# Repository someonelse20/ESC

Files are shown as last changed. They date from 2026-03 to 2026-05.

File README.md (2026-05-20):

# ESC

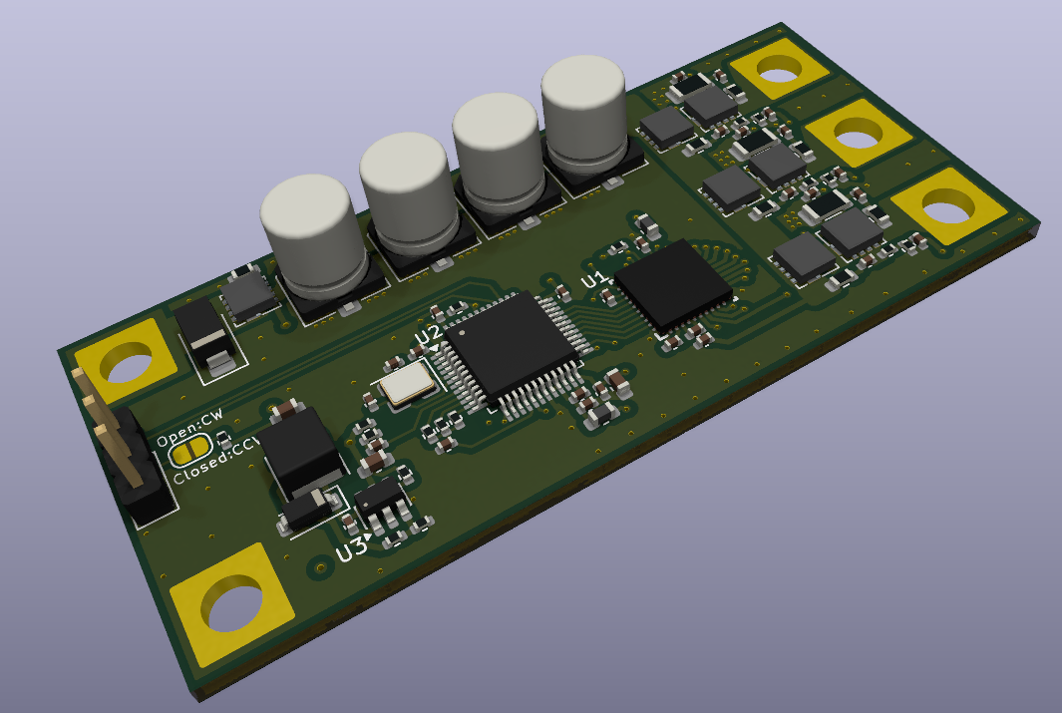
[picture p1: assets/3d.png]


A custom designed electronic speed controller that supports up to 7 cell LiPo batteries with 30 amps (untested).
I made this as part of my overall project of making a drone from scratch.

## Pinout

| Pin # | Function  |
| ----- | --- |
| 1 | PWM IN |
| 2 | Direction |
| 3 | GND |

Pull the Direction pin low (default) for clockwise rotation or high (3.3v) for counter clockwise rotation.
Alternatively, leave the solder bridge on the bottom of the board open for clockwise and closed for counter clockwise.

## PCB Layout

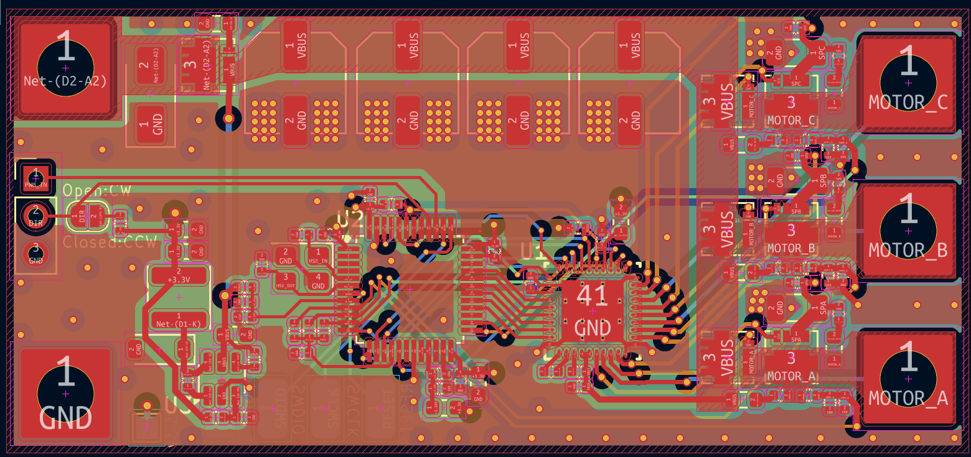
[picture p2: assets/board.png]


## Schematic

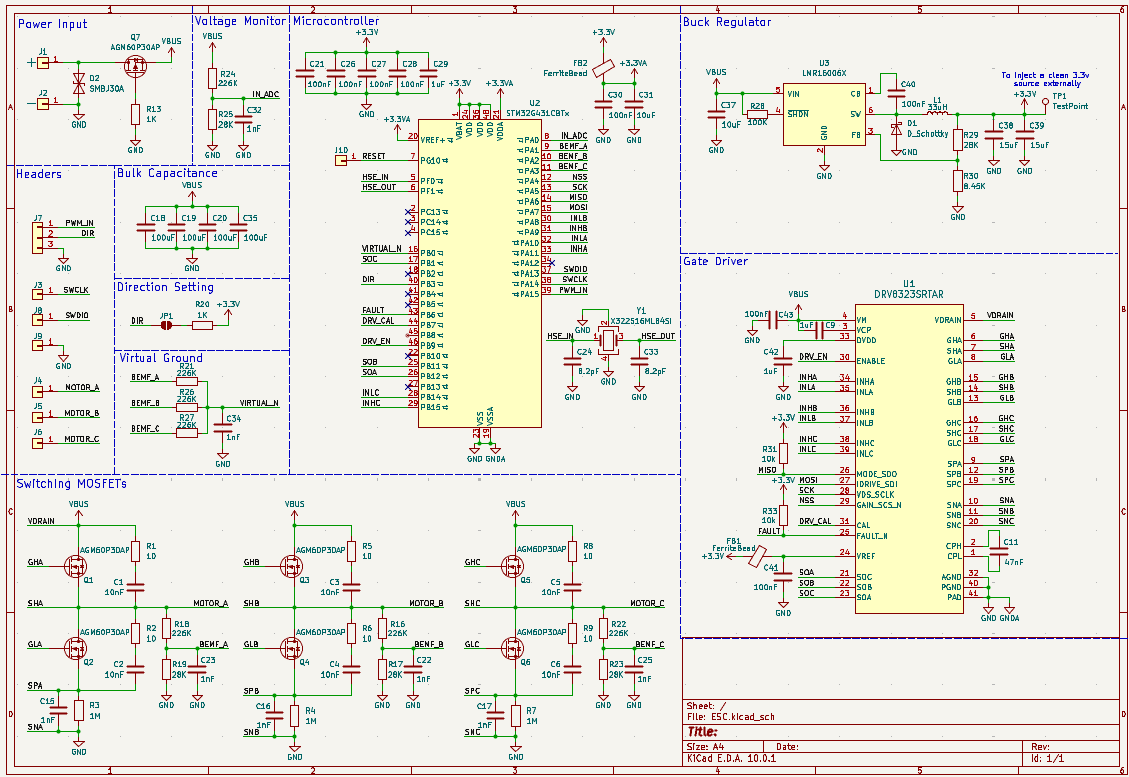
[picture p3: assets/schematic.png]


## BOM

| Name | Purpose | Quantity | Total Cost (USD) | Link | Distributor |
| --- | --- | --- | --- | --- | --- |
| PCB | 	The Circuit Board | 5 | 7.00 | [JLCPCB](https://jlcpcb.com/) | JLCPCB |
| PCB Assembly | Assembly for the board | 2 | 78.46 | [JLCPCB](https://jlcpcb.com/) | JLCPCB |

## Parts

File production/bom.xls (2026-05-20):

JLCPCB BOM Tool - BOM Matching
BOM name：bom-JLCPCB Assembly Order.xlsx |  |  | Download Time：2026-05-20 23:46:29 |  |  |  | * Our matching results are updated in real-time, but stock and prices may change. If it's been over 24 hours, please re-match before placing your order.
PCB Assembled Qty：5 |  |  | Est. Total Price：20.6320
Your BOM |  |  |  |  | Matched Parts |  |  |  |  |  |  | Order Information
Top Designator | Bottom Designator | Comment | Footprint | JLCPCB Part # | Matches | Part # | Manufacturer | Footprint | Description | Category | Warning | JLCPCB Part # | Product link | Lib Type | Qty | Source | Total Price ($)
C1,C2,C3,C4,C5,C6 |  | 10nF | 0402 |  | Select by System | CL05B103KB5NNNC | Samsung Electro-Mechanics | 0402 | 10nF 50V X7R ±10% 0402 Multilayer Ceramic Capacitors MLCC - SMD/SMT ROHS | Multilayer Ceramic Capacitors MLCC - SMD/SMT |  | C15195 | https://jlcpcb.com/partdetail/15869-CL05B103KB5NNNC/C15195 | Basic | 12 | 12 JLCPCB | 0.0192
C11 |  | 47nF | 0402 |  | Select by System | 0402B473K500NT | FH (Guangdong Fenghua Advanced Tech) | 0402 | 47nF 50V X7R ±10% 0402 Multilayer Ceramic Capacitors MLCC - SMD/SMT ROHS | Multilayer Ceramic Capacitors MLCC - SMD/SMT |  | C82219 | https://jlcpcb.com/partdetail/83376-0402B473K500NT/C82219 | Extended | 20 | 20 JLCPCB | 0.04
C15,C16,C17,C22,C23,C25,C32,C34 |  | 1nF | 0402 |  | Select by System | 0402B102K500NT | FH (Guangdong Fenghua Advanced Tech) | 0402 | 1nF 50V X7R ±10% 0402 Multilayer Ceramic Capacitors MLCC - SMD/SMT ROHS | Multilayer Ceramic Capacitors MLCC - SMD/SMT |  | C1523 | https://jlcpcb.com/partdetail/1875-0402B102K500NT/C1523 | Basic | 16 | 16 JLCPCB | 0.0208
C18,C19,C20,C35 |  | 100uF | C_Elec_6.3x7.7 |  | Select by Customer | RVT1V101M0607 | Honor Elec | SMD,D6.3xL7.7mm | -55℃~+105℃ 100uF 2000hrs@105℃ 35V 6.3mm 7.7mm ±20% SMD,D6.3xL7.7mm Aluminum Electrolytic Capacitors - SMD ROHS | Aluminum Electrolytic Capacitors - SMD |  | C3339 | https://jlcpcb.com/partdetail/HonorElec-RVT1V101M0607/C3339 | Extended | 10 | 10 JLCPCB | 0.377
C21,C26,C27,C28,C30,C40,C41,C43 |  | 100nF | 0402 |  | Select by Customer | GMK105BJ104KV-F | Taiyo Yuden | 0402 | 100nF 35V X5R ±10% 0402 Multilayer Ceramic Capacitors MLCC - SMD/SMT ROHS | Multilayer Ceramic Capacitors MLCC - SMD/SMT |  | C187828 | https://jlcpcb.com/partdetail/TaiyoYuden-GMK105BJ104KVF/C187828 | Extended | 24 | 24 JLCPCB | 0.1344
C24,C33 |  | 8.2pF | 0402 |  | Select by System | 0402CG8R2C500NT | FH (Guangdong Fenghua Advanced Tech) | 0402 | 50V 8.2pF C0G 0402 Multilayer Ceramic Capacitors MLCC - SMD/SMT ROHS | Multilayer Ceramic Capacitors MLCC - SMD/SMT |  | C1579 | https://jlcpcb.com/partdetail/1931-0402CG8R2C500NT/C1579 | Extended | 20 | 20 JLCPCB | 0.026
C29 |  | 1uF | 0603 |  | Select by System | CL10A105KB8NNNC | Samsung Electro-Mechanics | 0603 | 1uF 50V X5R ±10% 0603 Multilayer Ceramic Capacitors MLCC - SMD/SMT ROHS | Multilayer Ceramic Capacitors MLCC - SMD/SMT |  | C15849 | https://jlcpcb.com/partdetail/16531-CL10A105KB8NNNC/C15849 | Basic | 2 | 2 JLCPCB | 0.0152
C31 |  | 10uF | 0402 |  | Select by System | CL05A106MQ5NUNC | Samsung Electro-Mechanics | 0402 | 10uF 6.3V X5R ±20% 0402 Multilayer Ceramic Capacitors MLCC - SMD/SMT ROHS | Multilayer Ceramic Capacitors MLCC - SMD/SMT |  | C15525 | https://jlcpcb.com/partdetail/16204-CL05A106MQ5NUNC/C15525 | Basic | 2 | 2 JLCPCB | 0.0136
C37 |  | 10uF | 0603 |  | Select by System | CL10A106KP8NNNC | Samsung Electro-Mechanics | 0603 | 10V 10uF X5R ±10% 0603 Multilayer Ceramic Capacitors MLCC - SMD/SMT ROHS | Multilayer Ceramic Capacitors MLCC - SMD/SMT |  | C19702 | https://jlcpcb.com/partdetail/20411-CL10A106KP8NNNC/C19702 | Basic | 2 | 2 JLCPCB | 0.0204
C38,C39 |  | 15uF | 0603 |  | Select by System | C1608X5R0J156MT000E | TDK | 0603 | 15uF 6.3V X5R ±20% 0603 Multilayer Ceramic Capacitors MLCC - SMD/SMT ROHS | Multilayer Ceramic Capacitors MLCC - SMD/SMT |  | C445715 | https://jlcpcb.com/partdetail/TDK-C1608X5R0J156MT000E/C445715 | Extended | 6 | 6 JLCPCB | 0.501
C42,C9 |  | 1uF | 0402 |  | Select by Customer | CL05A105KL5NRNC | Samsung Electro-Mechanics | 0402 | 1uF 35V X5R ±10% 0402 Multilayer Ceramic Capacitors MLCC - SMD/SMT ROHS | Multilayer Ceramic Capacitors MLCC - SMD/SMT |  | C307413 | https://jlcpcb.com/partdetail/291087-CL05A105KL5NRNC/C307413 | Extended | 20 | 20 JLCPCB | 0.34
D1 |  | D_Schottky | D_SOD-123 |  | Select by Customer | PMEG6010CEH,115 | Nexperia | SOD-123F | 1 Independent 1A 50uA@60V 60V 660mV@1A 9A SOD-123F Schottky Diodes ROHS | Schottky Diodes |  | C110797 | https://jlcpcb.com/partdetail/Nexperia-PMEG6010CEH115/C110797 | Extended | 6 | 6 JLCPCB | 2.0862
D2 |  | SMBJ30A | D_SMA |  | Select by System | SMBJ30A | YFW | DO-214AA(SMB) | -65℃~+150℃ 12.4A 1uA 30V 36.8V 390pF 48.4V 600W@10/1000us TVS Unidirectional DO-214AA(SMB) ESD and Surge Protection (TVS/ESD) ROHS | ESD And Surge Protection (TVS/ESD) |  | C3013760 | https://jlcpcb.com/partdetail/YFW-SMBJ30A/C3013760 | Extended | 6 | 6 JLCPCB | 0.2886
FB1,FB2 |  | FerriteBead | 0603 |  | Select by Customer | GZ1608D601TF | Sunlord | 0603 | -55℃~+125℃ 1 200mA 450mΩ 600Ω@100MHz ±25% 0603 Ferrite Beads ROHS | Ferrite Beads |  | C1002 | https://jlcpcb.com/partdetail/Sunlord-GZ1608D601TF/C1002 | Basic | 4 | 4 JLCPCB | 0.0744
L1 |  | 27uH | L_APV_ANR4030 |  | Select by Customer | ANR4030T330M | APV | SMD,4x4mm | 1.2A 33uH 920mA Magnetic Shielded Inductor ±20% SMD,4x4mm Power Inductors ROHS | Power Inductors |  | C7497082 | https://jlcpcb.com/partdetail/APV-ANR4030T330M/C7497082 | Extended | 5 | 5 JLCPCB | 0.214
Q1,Q2,Q3,Q4,Q5,Q6 |  | AGM60P30AP | D_QFN_3.3x3.3mm_P0.65mm |  | Unconfirmed | AGM60P30AP | AGM-Semi | PDFN-8(3.3x3.3) | -55℃~+150℃ 1 P-Channel 1.6V 114pF 11pF 30A 35W 40mΩ@10V 60V 740pF 9.8nC@10V P-Channel PDFN-8(3.3x3.3) MOSFETs ROHS | MOSFETs | 1.Multiple lines in the BOM have been matched to the same part. Please check if the matching is correct. ; | C20625923 | https://jlcpcb.com/partdetail/AGMSemi-AGM60P30AP/C20625923 | Extended | 14 | 14 JLCPCB | 2.6096
Q7 |  | AGM60P30A | D_QFN_3.3x3.3mm_P0.65mm |  | Select by Customer | AGM60P30AP | AGM-Semi | PDFN-8(3.3x3.3) | -55℃~+150℃ 1 P-Channel 1.6V 114pF 11pF 30A 35W 40mΩ@10V 60V 740pF 9.8nC@10V P-Channel PDFN-8(3.3x3.3) MOSFETs ROHS | MOSFETs | 1.Multiple lines in the BOM have been matched to the same part. Please check if the matching is correct. ; | C20625923 | https://jlcpcb.com/partdetail/AGMSemi-AGM60P30AP/C20625923 | Extended | 14 | 14 JLCPCB | 2.6096
R1,R2,R5,R6,R8,R9 |  | 10 | 0603 |  | Unconfirmed | 0603WAF100JT5E | UNI-ROYAL(Uniroyal Elec) | 0603 | -55℃~+155℃ 100mW 10Ω 75V Thick Film Resistor ±1% ±400ppm/℃ 0603 Chip Resistor - Surface Mount ROHS | Chip Resistor - Surface Mount | 1.The comment (0603WAF100JT5E) of this part does not match the one (10) provided in your BOM. Please confirm; | C22859 | https://jlcpcb.com/partdetail/23586-0603WAF100JT5E/C22859 | Basic | 12 | 12 JLCPCB | 0.0228
R3,R4,R7 |  | 1M | 1206 |  | Unconfirmed | 1206W4F1004T5E | UNI-ROYAL(Uniroyal Elec) | 1206 | -55℃~+155℃ 1MΩ 200V 250mW Thick Film Resistor ±1% ±100ppm/℃ 1206 Chip Resistor - Surface Mount ROHS | Chip Resistor - Surface Mount | 1.The comment (1206W4F1004T5E) of this part does not match the one (1M) provided in your BOM. Please confirm; | C17927 | https://jlcpcb.com/partdetail/18615-1206W4F1004T5E/C17927 | Basic | 6 | 6 JLCPCB | 0.0258
R13 |  | 1K | 0603 |  | Unconfirmed | 0603WAF1001T5E | UNI-ROYAL(Uniroyal Elec) | 0603 | -55℃~+155℃ 100mW 1kΩ 75V Thick Film Resistor ±1% ±100ppm/℃ 0603 Chip Resistor - Surface Mount ROHS | Chip Resistor - Surface Mount | 1.The comment (0603WAF1001T5E) of this part does not match the one (1K) provided in your BOM. Please confirm; | C21190 | https://jlcpcb.com/partdetail/21904-0603WAF1001T5E/C21190 | Basic | 2 | 2 JLCPCB | 0.0032
R16,R18,R21,R22,R24,R26,R27 |  | 226K | 0402 |  | Unconfirmed | CR0402FF2263G | LIZ Elec | 0402 | -55℃~+125℃ 226kΩ 50V 62.5mW Thick Film Resistor ±1% ±200ppm/℃ 0402 Chip Resistor - Surface Mount ROHS | Chip Resistor - Surface Mount | 1.The comment (CR0402FF2263G) of this part does not match the one (226K) provided in your BOM. Please confirm; | C100317 | https://jlcpcb.com/partdetail/LIZElec-CR0402FF2263G/C100317 | Extended | 24 | 24 JLCPCB | 0.0144
R17,R19,R23,R25,R29 |  | 28K | 0402 |  | Unconfirmed | FRC0402F2802TS | FOJAN | 0402 | -55℃~+155℃ 28kΩ 50V 62.5mW Thick Film Resistor ±1% ±100ppm/℃ 0402 Chip Resistor - Surface Mount ROHS | Chip Resistor - Surface Mount | 1.The comment (FRC0402F2802TS) of this part does not match the one (28K) provided in your BOM. Please confirm; | C2998150 | https://jlcpcb.com/partdetail/FOJAN-FRC0402F2802TS/C2998150 | Extended | 20 | 20 JLCPCB | 0.012
R20 |  | 1K | 0402 |  | Unconfirmed | 0402WGF1001TCE | UNI-ROYAL(Uniroyal Elec) | 0402 | -55℃~+155℃ 1kΩ 50V 62.5mW Thick Film Resistor ±1% ±100ppm/℃ 0402 Chip Resistor - Surface Mount ROHS | Chip Resistor - Surface Mount | 1.The comment (0402WGF1001TCE) of this part does not match the one (1K) provided in your BOM. Please confirm; | C11702 | https://jlcpcb.com/partdetail/12256-0402WGF1001TCE/C11702 | Basic | 2 | 2 JLCPCB | 0.002
R28 |  | 100K | 0402 |  | Unconfirmed | 0402WGF1003TCE | UNI-ROYAL(Uniroyal Elec) | 0402 | -55℃~+155℃ 100kΩ 50V 62.5mW Thick Film Resistor ±1% ±100ppm/℃ 0402 Chip Resistor - Surface Mount ROHS | Chip Resistor - Surface Mount | 1.The comment (0402WGF1003TCE) of this part does not match the one (100K) provided in your BOM. Please confirm; | C25741 | https://jlcpcb.com/partdetail/26484-0402WGF1003TCE/C25741 | Basic | 2 | 2 JLCPCB | 0.0018
R30 |  | 8.45K | 0402 |  | Unconfirmed | RC0402FR-078K45L | YAGEO | 0402 | -55℃~+155℃ 50V 62.5mW 8.45kΩ Thick Film Resistor ±1% ±100ppm/℃ 0402 Chip Resistor - Surface Mount ROHS | Chip Resistor - Surface Mount | 1.The comment (RC0402FR-078K45L) of this part does not match the one (8.45K) provided in your BOM. Please confirm; | C185388 | https://jlcpcb.com/partdetail/YAGEO-RC0402FR078K45L/C185388 | Extended | 20 | 20 JLCPCB | 0.016
R31,R33 |  | 10k | 0402 |  | Unconfirmed | 0402WGF1002TCE | UNI-ROYAL(Uniroyal Elec) | 0402 | -55℃~+155℃ 10kΩ 50V 62.5mW Thick Film Resistor ±1% ±100ppm/℃ 0402 Chip Resistor - Surface Mount ROHS | Chip Resistor - Surface Mount | 1.The comment (0402WGF1002TCE) of this part does not match the one (10k) provided in your BOM. Please confirm; | C25744 | https://jlcpcb.com/partdetail/26487-0402WGF1002TCE/C25744 | Basic | 4 | 4 JLCPCB | 0.0052
U1 |  | DRV8323SRTAR | DRV8323SRTAR |  | Select by System | DRV8323SRTAR | Texas Instruments | WQFN-40-EP(6x6) | -40℃~+125℃ 12uA 1A 3 6V~60V SPI Three Phase WQFN-40-EP(6x6) Brushless DC (BLDC) Motor Driver ROHS | Global Sourcing Parts |  | C701784 | https://jlcpcb.com/partdetail/TexasInstruments-DRV8323SRTAR/C701784 | Extended | 2 | 2 JLCPCB | 3.4794
U2 |  | STM32G431CBTx | LQFP-48_7x7mm_P0.5mm |  | Select by Customer | STM32G431CBT6 | STMicroelectronics | LQFP-48(7x7) | -40℃~+85℃ 1.71V~3.6V 128KB 12bit 12bit 170MHz 32 Bit 32KB 38 ARM Cortex-M4F Built-in FLASH LQFP-48(7x7) Microcontrollers (MCU/MPU/SOC) ROHS | Microcontrollers (MCU/MPU/SOC) |  | C529355 | https://jlcpcb.com/partdetail/STMicroelectronics-STM32G431CBT6/C529355 | Extended | 2 | 2 JLCPCB | 6.3982
U3 |  | LMR16006X | SOT-23-6 |  | Select by System | LMR16006XDDCR | Texas Instruments | SOT-6 | -40℃~+125℃@(TJ) 1 28uA 4V~60V 600mA 700kHz 765mV~55V Adjustable Buck Buck Built-in No SOT-6 DC-DC Converters ROHS | DC-DC Converters |  | C87080 | https://jlcpcb.com/partdetail/TexasInstruments-LMR16006XDDCR/C87080 | Extended | 2 | 2 JLCPCB | 1.1182
Y1 |  | X322516MLB4SI | Crystal_SMD_3225-4Pin_3.2x2.5mm |  | Select by System | X322516MLB4SI | YXC Crystal Oscillators | SMD3225-4P | -40℃~+85℃ 16MHz 9pF Crystal Oscillator ±10ppm ±20ppm SMD3225-4P Crystals ROHS | Crystals |  | C13738 | https://jlcpcb.com/partdetail/YXC_CrystalOscillators-X322516MLB4SI/C13738 | Basic | 2 | 2 JLCPCB | 0.143
J1,J4,J5,J6 |  | + | SolderWire-4sqmm_1x01_D3mm_OD6mm |  | No matches | No Part Selected
J2 |  | - | SolderWire-4sqmm_1x01_D3mm_OD6mm |  | No matches | No Part Selected
J7 |  | Conn_01x03 | PinHeader_1x03_P2.54mm_Vertical |  | No matches | No Part Selected

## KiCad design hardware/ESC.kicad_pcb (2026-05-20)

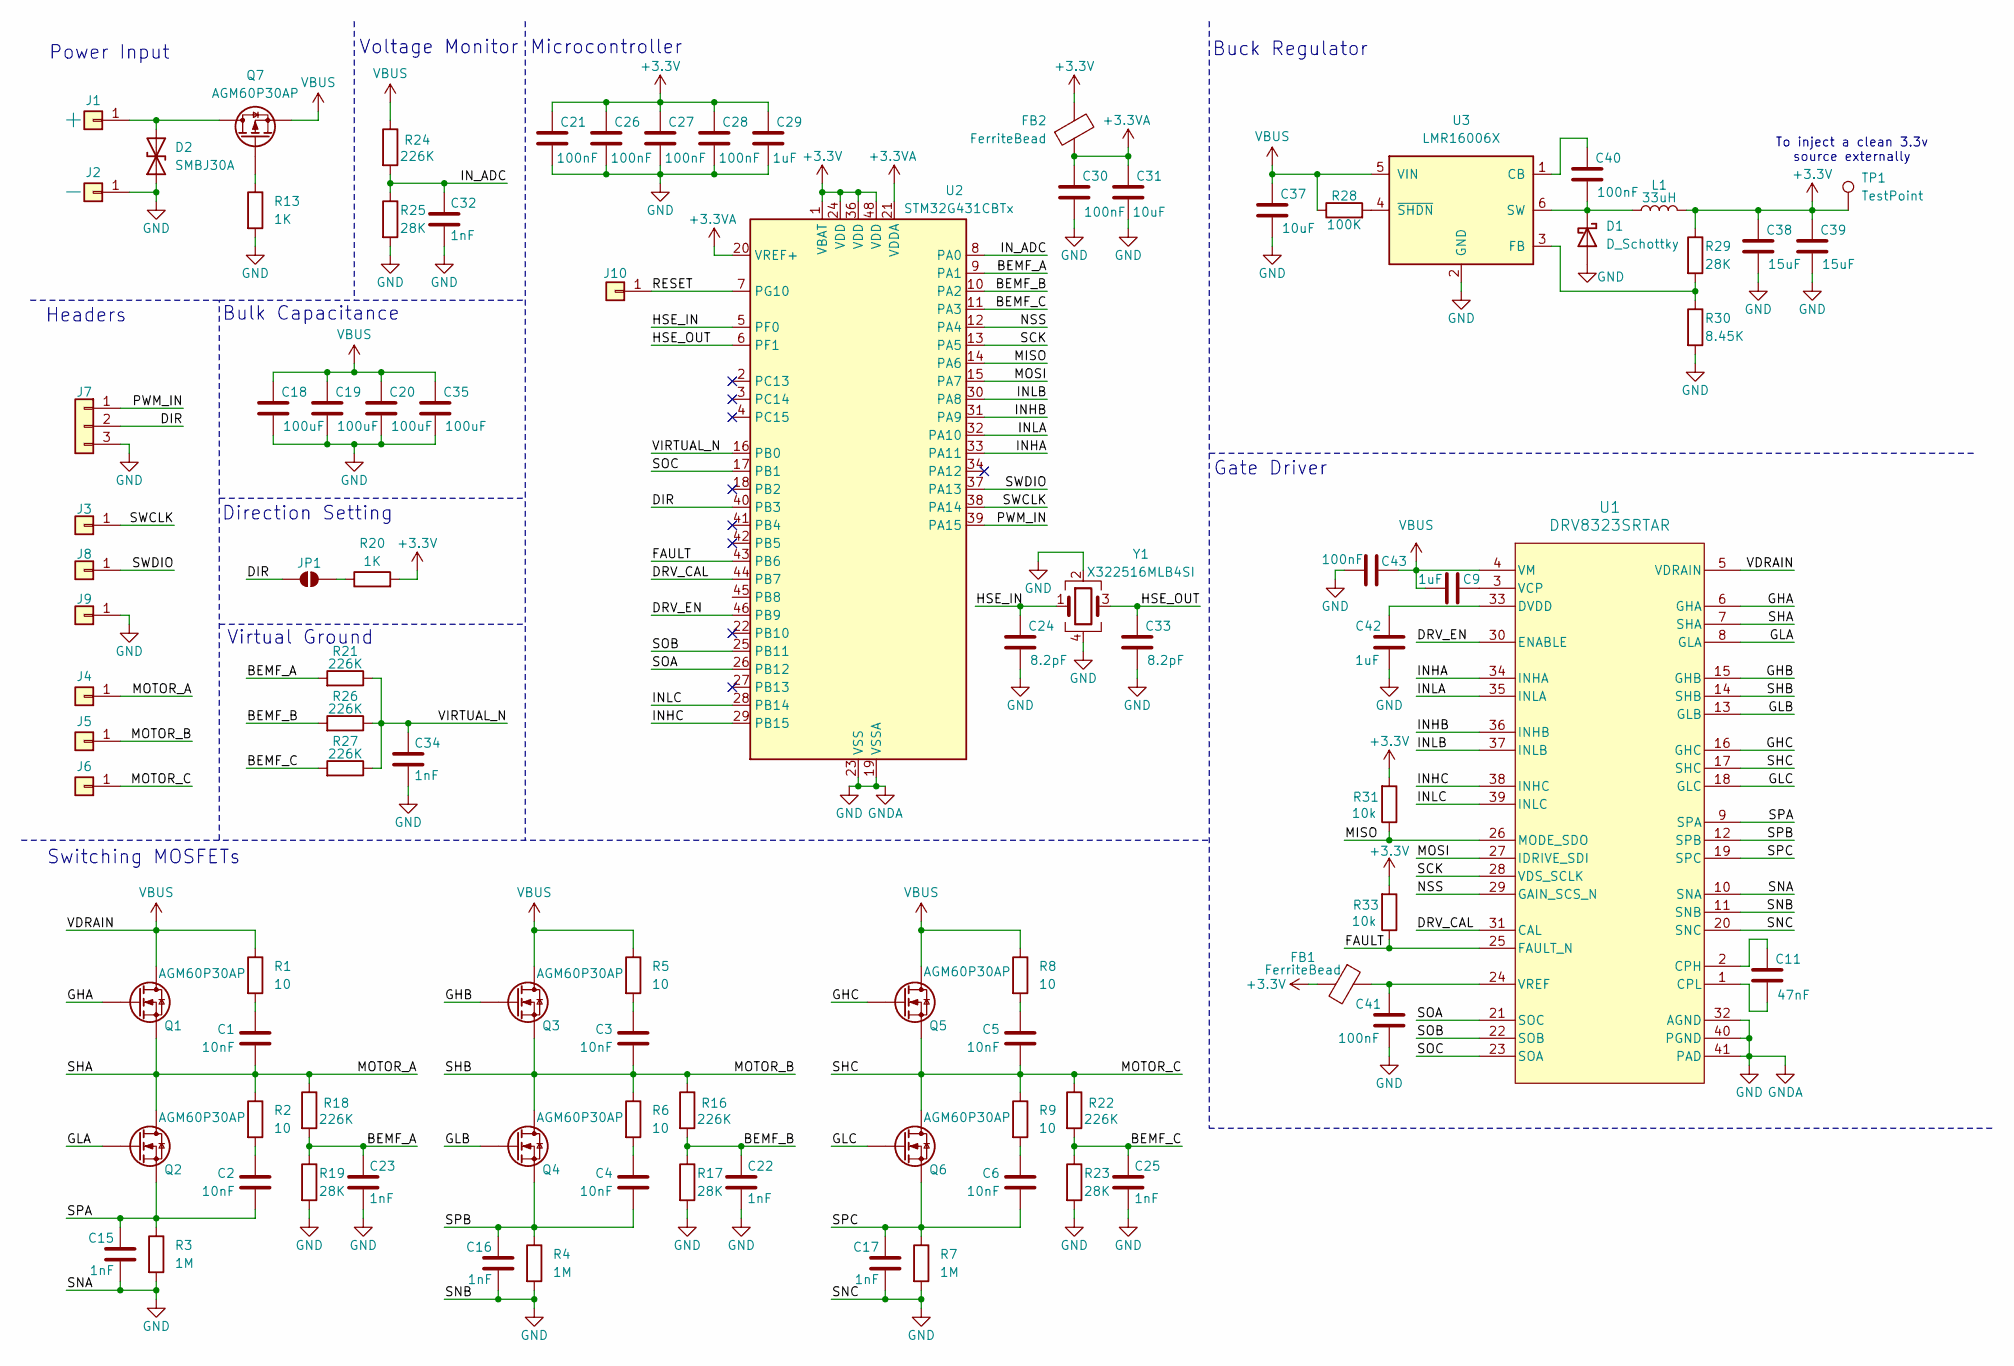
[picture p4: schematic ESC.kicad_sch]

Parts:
C1, C2, C3, C4, C5, C6: 10nF; C_0402_1005Metric
C9, C42: 1uF; C_0402_1005Metric
C11: 47nF; C_0402_1005Metric
C15, C16, C17, C22, C23, C25, C32, C34: 1nF; C_0402_1005Metric
C18, C19, C20, C35: 100uF; C_Elec_6.3x7.7
C21, C26, C27, C28, C30, C40, C41, C43: 100nF; C_0402_1005Metric
C24, C33: 8.2pF; C_0402_1005Metric
C29: 1uF; C_0603_1608Metric
C31: 10uF; C_0402_1005Metric
C37: 10uF; C_0603_1608Metric
C38, C39: 15uF; C_0603_1608Metric
D1: D_Schottky; D_SOD-123
D2: SMBJ30A; D_SMA
FB1, FB2: FerriteBead; L_0603_1608Metric
J1, J4, J5, J6: +; SolderWire-4sqmm_1x01_D3mm_OD6mm
J2: -; SolderWire-4sqmm_1x01_D3mm_OD6mm
J3, J8, J9, J10: +; SolderWirePad_1x01_SMD_2x4mm
J7: Conn_01x03; PinHeader_1x03_P2.54mm_Vertical
JP1: SolderJumper_2_Open; SolderJumper-2_P1.3mm_Open_RoundedPad1.0x1.5mm
L1: 33uH; L_APV_ANR4030
Q1, Q2, Q3, Q4, Q5, Q6, Q7: AGM60P30AP; D_QFN_3.3x3.3mm_P0.65mm
R1, R2, R5, R6, R8, R9: 10; R_0603_1608Metric
R3, R4, R7: 1M; R_1206_3216Metric
R13: 1K; R_0603_1608Metric
R16, R18, R21, R22, R24, R26, R27: 226K; R_0402_1005Metric
R17, R19, R23, R25, R29: 28K; R_0402_1005Metric
R20: 1K; R_0402_1005Metric
R28: 100K; R_0402_1005Metric
R30: 8.45K; R_0402_1005Metric
R31, R33: 10k; R_0402_1005Metric
TP1: TestPoint; TestPoint_Pad_1.5x1.5mm
U1: DRV8323SRTAR
U2: STM32G431CBTx; LQFP-48_7x7mm_P0.5mm
U3: LMR16006X; SOT-23-6
Y1: X322516MLB4SI; Crystal_SMD_3225-4Pin_3.2x2.5mm

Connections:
+3.3V: C21.1, C26.1, C27.1, C28.1, C29.1, C38.1, C39.1, FB1.2, FB2.2, L1.2, R20.2, R29.1, R31.2, R33.2, TP1.1 (1_1), U2.1 (VBAT), U2.24 (VDD), U2.36 (VDD), U2.48 (VDD)
+3.3VA: C30.1, C31.1, FB2.1, U2.20 (VREF+), U2.21 (VDDA)
/BEMF_A: C23.1, R18.2, R19.1, R21.2, U2.9 (PA1)
/BEMF_B: C22.1, R16.2, R17.1, R26.2, U2.10 (PA2)
/BEMF_C: C25.1, R22.2, R23.1, R27.2, U2.11 (PA3)
/DIR: J7.2, JP1.1 (A), U2.40 (PB3)
/DRV_CAL: U1.31 (CAL), U2.44 (PB7)
/DRV_EN: U1.30 (ENABLE), U2.46 (PB9)
/FAULT: R33.1, U1.25 (FAULT_N), U2.43 (PB6)
/GHA: Q1.2 (G), U1.6 (GHA)
/GHB: Q3.2 (G), U1.15 (GHB)
/GHC: Q5.2 (G), U1.16 (GHC)
/GLA: Q2.2 (G), U1.8 (GLA)
/GLB: Q4.2 (G), U1.13 (GLB)
/GLC: Q6.2 (G), U1.18 (GLC)
/HSE_IN: C24.1, U2.5 (PF0), Y1.1
/HSE_OUT: C33.1, U2.6 (PF1), Y1.3
/INHA: U1.34 (INHA), U2.33 (PA11)
/INHB: U1.36 (INHB), U2.31 (PA9)
/INHC: U1.38 (INHC), U2.29 (PB15)
/INLA: U1.35 (INLA), U2.32 (PA10)
/INLB: U1.37 (INLB), U2.30 (PA8)
/INLC: U1.39 (INLC), U2.28 (PB14)
/IN_ADC: C32.1, R24.2, R25.1, U2.8 (PA0)
/MISO: R31.1, U1.26 (MODE_SDO), U2.14 (PA6)
/MOSI: U1.27 (IDRIVE_SDI), U2.15 (PA7)
/MOTOR_A: C1.2, J4.1 (Pin_1_1), Q1.1 (S), Q2.3 (D), R2.1, R18.1, U1.7 (SHA)
/MOTOR_B: C3.2, J5.1 (Pin_1_1), Q3.1 (S), Q4.3 (D), R6.1, R16.1, U1.14 (SHB)
/MOTOR_C: C5.2, J6.1 (Pin_1_1), Q5.1 (S), Q6.3 (D), R9.1, R22.1, U1.17 (SHC)
/NSS: U1.29 (GAIN_SCS_N), U2.12 (PA4)
/PWM_IN: J7.1, U2.39 (PA15)
/RESET: J10.1 (Pin_1_1), U2.7 (PG10)
/SCK: U1.28 (VDS_SCLK), U2.13 (PA5)
/SOA: U1.21 (SOC), U2.26 (PB12)
/SOB: U1.22 (SOB), U2.25 (PB11)
/SOC: U1.23 (SOA), U2.17 (PB1)
/SPA: C2.2, C15.1, Q2.1 (S), R3.1, U1.9 (SPA)
/SPB: C4.2, C16.1, Q4.1 (S), R4.1, U1.12 (SPB)
/SPC: C6.2, C17.1, Q6.1 (S), R7.1, U1.19 (SPC)
/SWCLK: J3.1 (Pin_1_1), U2.38 (PA14)
/SWDIO: J8.1 (Pin_1_1), U2.37 (PA13)
/VIRTUAL_N: C34.1, R21.1, R26.1, R27.1, U2.16 (PB0)
GND: C15.2, C16.2, C17.2, C18.2, C19.2, C20.2, C21.2, C22.2, C23.2, C24.2, C25.2, C26.2, C27.2, C28.2, C29.2, C30.2, C31.2, C32.2, C33.2, C34.2, C35.2, C37.2, C38.2, C39.2, C41.2, C42.2, C43.2, D1.2 (A), D2.1 (A1), J2.1 (Pin_1_1), J7.3, J9.1 (Pin_1_1), R3.2, R4.2, R7.2, R13.2, R17.2, R19.2, R23.2, R25.2, R30.2, U1.10 (SNA), U1.11 (SNB), U1.20 (SNC), U1.32 (AGND), U1.40 (PGND), U1.41 (PAD), U2.19 (VSSA), U2.23 (VSS), U2.35 (VSS), U2.47 (VSS), U3.2 (GND), Y1.2, Y1.4
unnamed: C1.1, R1.2
unnamed: C2.1, R2.2
unnamed: C3.1, R5.2
unnamed: C4.1, R6.2
unnamed: C5.1, R8.2
unnamed: C6.1, R9.2
unnamed: C40.2, D1.1 (K), L1.1, U3.6 (SW)
unnamed: D2.2 (A2), J1.1 (Pin_1_1), Q7.3 (D)
unnamed: JP1.2 (B), R20.1
unnamed: Q7.2 (G), R13.1
unnamed: C11.1, U1.2 (CPH)
unnamed: C11.2, U1.1 (CPL)
unnamed: C42.1, U1.33 (DVDD)
unnamed: C9.2, U1.3 (VCP)
unnamed: C41.1, FB1.1, U1.24 (VREF)
unnamed: C40.1, U3.1 (CB)
unnamed: R29.2, R30.1, U3.3 (FB)
unnamed: R28.2, U3.4 (~SHDN)
VBUS: C9.1, C18.1, C19.1, C20.1, C35.1, C37.1, C43.1, Q1.3 (D), Q3.3 (D), Q5.3 (D), Q7.1 (S), R1.1, R5.1, R8.1, R24.1, R28.1, U1.4 (VM), U1.5 (VDRAIN), U3.5 (VIN)

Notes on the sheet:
Buck Regulator
Bulk Capacitance
Switching MOSFETs
To inject a clean 3.3v source externally
Power Input
Microcontroller
Direction Setting
Virtual Ground
Voltage Monitor
Gate Driver
Headers

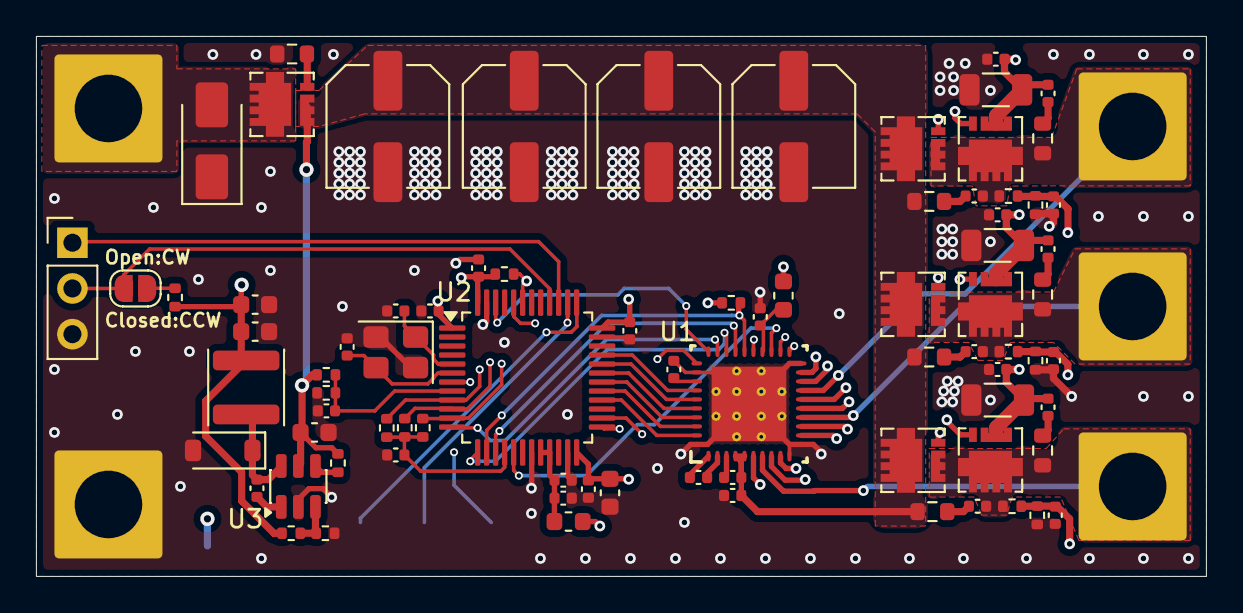
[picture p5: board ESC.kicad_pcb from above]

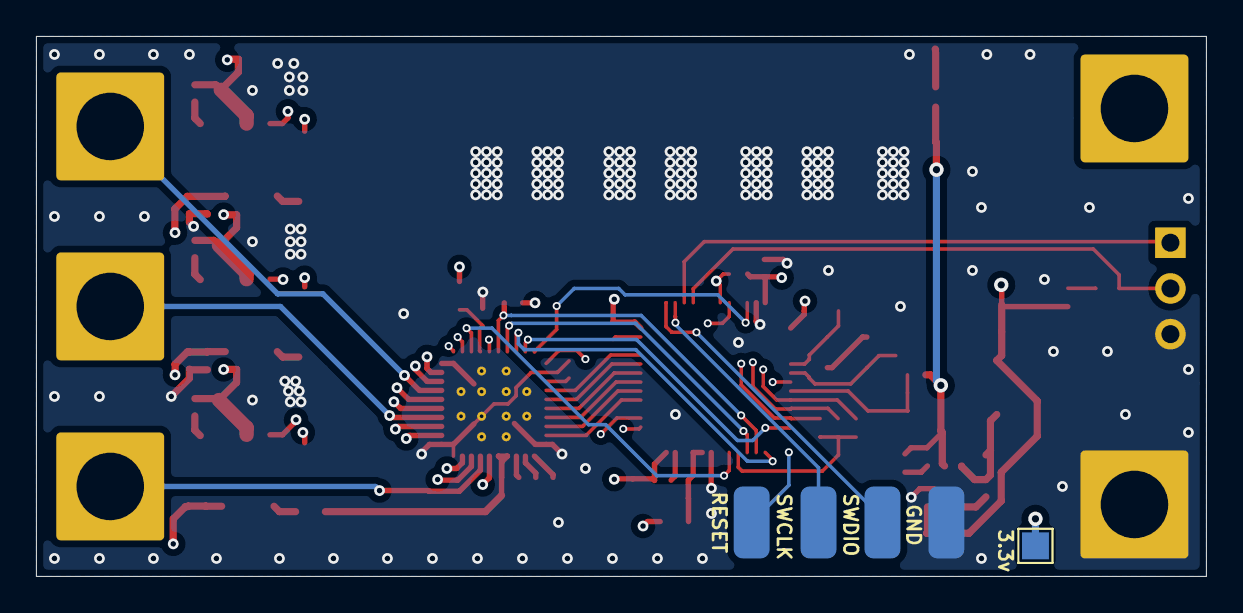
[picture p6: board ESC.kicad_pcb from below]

Board: 4 copper layers, 65.0 x 30.0 mm, 91 parts (5 on the bottom side), 62 nets.

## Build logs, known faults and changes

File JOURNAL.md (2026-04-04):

<!--
  This journal is auto generated by Stasis.
-->

# 4/1/2026 4 PM - Wrote Firmware

_Time spent: 7h_

I wrote all the firmware to get the esc running. At first I was looking at implementing a field oriented controll algorithm but this would drive all three phases at once and not leave any floating to measure the back emf voltage. From what I could find the back emf can still be found by measuring the current but I couldn't find out how. I settled on trapezoidal controll which is simpler and would always leave a phase floating to measure the back emf. To control the speed I used a pid library I wrote a while ago. The actual algorithm is pretty simple and my main loop is only about 12 lines long. I'm not even using the rotor angle and will probably remove it eventualy. 

Since I decided to not use field oriented control I don't need to measure the current but I still wrote a function to do so. After looking at the datasheet for the gate driver I realized that all the default settings are fine for what I need so I don't need to confgure it at startup. I have a half finished header file for a driver I was going to write for this. 

One quick side project I had was to resize all of the small vias to make them large enough so I don't get an extra fee from jlcpcb. I also increased the track width for the mosfet gate traces.








# 3/25/2026 5 PM - Made PCB

_Time spent: 4h_


I made the pcb and it was pretty hard to fit it all in a small space. If I were to try to design another version or make it smaller I would consider going for 6 layers instead of 4. 

I placed the bulk capacitors at the top of the board with copper fills for traces and lots of vias to allow plenty of current to flow through. I placed the stm32 on the top layer and the mosfets, gate driver, and regulator components on the bottom layer.



I also added a jumper to select the motor direction in addition to a pin header and pads for serial wire debug and reset for programming. I added pads because there wasn't space for pins between all the layers. I also added vias on the vbus mosfet pads which isn't optimal but the only option I had to save space. The traces between the mosfets and from the mosfets to ground are much smaller than the traces going in but although all the parts are rated for 30 amps I only realisticaly expect to need 5 or so.






# 3/23/2026 3 PM - Finished Most of Schematic

_Time spent: 6h_

To finish the schematic I had to do a lot of background research to know what is actually hapenning. One of the more important parts is sensing the back emf signal to determine the position of the rotor to know when to switch to the next step in the 6 step sequence. Conveniently when the back emf (bemf) voltage crosses zero is the most efficient time to switch to the next step. Unconveniently the voltage is refrenced to the ground in the motor which we do not know. This can be solved by delaying switching steps by about 30 degrees of the motor or simulating the virtual ground. I wasn't sure what to do so I added the hardware for the virtual ground in case I wanted it. 

I then added the rest of the schematic and added all the parts for the microcontroller. I decided to remove the inductor because it was so big. 

I assigned footprints and I think I might make it double sided even though it will be more expensive because I want it to be small enough to be mounted on a drone.






# 3/19/2026 10 PM - Selected Components and Started Schematic

_Time spent: 4h_

Designing a custom ESC looked like a cool chalange so I started researching and I found the DRV8323R gate driver from TI. I chose this one because it has a SPI interface so its settings can be changed on the fly and it has an integrated buck regulator so I won't have to add that too. I then chose the STM32G431CBT6 because looking online it seemed that the STM32 G4 series was made for things like this and this specific model seems to be popular on JLCPCB. I then wired up the external mosfets according to the gate driver datasheet. 
2026-03-19-184207_hyprshot
I then added the power source pins and added a TVS diode to protect from overvoltage and a p mosfet for reverse voltage protection. I then added an inductor and a bunch of capacitors to smooth the input supply. Later I want to find out if the inductor is strictly needed because it's really big and I want to make this as small as I can. 
2026-03-19-184217_hyprshot

2026-03-19-184200_hyprshot





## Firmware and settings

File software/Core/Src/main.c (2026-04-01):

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
/* Includes ------------------------------------------------------------------*/
#include "main.h"

/* USER CODE BEGIN Includes */
#include <stdbool.h>
#include <stddef.h>
#include <stdint.h>
#include <sys/types.h>

#include "pid.h"

/* USER CODE END Includes */

/* USER CODE BEGIN PD */

// Configuration define
#define HAL_TIMEOUT 100
#define MIN_RPM 100
#define MAX_RPM 1000
#define BEMF_MIN_MARGIN 0.1 // How much above zero the BEMF voltage needs to be to read
#define BEMF_MAX_MARGIN 1   // How much below sys voltage BEMF needs to be to read
#define SET_ROTOR_TIME 10   // How long to wait in ms to set rotor to position
#define MIN_DUTY_CYCLE 0.1  // Minimum pwm duty cycle to send to gate driver

// System define
#define SYS_VOLT_INDEX 0
#define BEMF_A_INDEX 1
#define BEMF_B_INDEX 2
#define BEMF_C_INDEX 3
#define CURRENT_A_INDEX 4
#define CURRENT_B_INDEX 6
#define CURRENT_C_INDEX 5
#define V_GND_INDEX 7
#define TEMP_INDEX 8

/* USER CODE END PD */

ADC_HandleTypeDef hadc1;
DMA_HandleTypeDef hdma_adc1;

SPI_HandleTypeDef hspi1;

TIM_HandleTypeDef htim1;
TIM_HandleTypeDef htim2;
TIM_HandleTypeDef htim15;

/* USER CODE BEGIN PV */

const uint32_t STARTUP_DELAY = MIN_RPM / 360000; // Convert RPM to 1/6 revolutions per ms

pid_control_t speed_pid;

double rotor_angle;
double prev_rotor_angle;
double prev_rotor_angle_time;
double prev_rotor_speed_time;
double zero_cross_time;
double rotor_speed;
double input_speed;

double rotor_current[3];
double rotor_bemf[3];
double prev_rotor_bemf[3];

int8_t dir;
int8_t sequence[6][3] = { // 1 is VCC, -1 is GND, and 0 is floating
	{1, -1, 0},
	{1, 0, -1},
	{0, 1, -1},
	{-1, 1, 0},
	{-1, 0, 1},
	{0, -1, 1}
};
volatile uint32_t *sequence_tim[3][2] = {
	{&TIM1->CCR4, &TIM1->CCR3},
	{&TIM1->CCR2, &TIM1->CCR1},
	{&TIM2->CCR2, &TIM2->CCR1},
};
uint32_t phase_angles[] = {0, 120, 240};
uint8_t step;
uint8_t floating;

uint32_t adc_buf[9];

/* USER CODE END PV */

void SystemClock_Config(void);
static void MX_GPIO_Init(void);
static void MX_DMA_Init(void);
static void MX_SPI1_Init(void);
static void MX_ADC1_Init(void);
static void MX_TIM1_Init(void);
static void MX_TIM15_Init(void);
static void MX_TIM2_Init(void);
/* USER CODE BEGIN PFP */

// Helper functions
static uint8_t sign(double value);
static float process_adc(uint32_t raw_value);
static float process_current(double raw_value);
static uint8_t check_valid_bemf(double bemf_v);
static double clamp(double value, double min, double max);
static double map(double value, double in_min, double in_max, double out_min, double out_max);

// Primary funcitons
static double get_rotor_angle(uint8_t floating, double rotor_speed);
static void get_rotor_bemf(double *rotor_bemf_p);
static void get_rotor_current(double *rotor_current_p);

static void drive_rotor(uint8_t step, double duty_cycle);
static void get_zero_crossing(double bemf[3], double prev_bemf[3]);

static void set_rotor(void);
static void startup_sequence(void);

/* USER CODE END PFP */

/**
 * @brief  The application entry point.
 * @retval int
 */
int main(void)
{

	/* USER CODE BEGIN 1 */
	reset_pid(&speed_pid);

	/* USER CODE END 1 */

	/* MCU Configuration--------------------------------------------------------*/

	/* Reset of all peripherals, Initializes the Flash interface and the Systick. */
	HAL_Init();

	/* Configure the system clock */
	SystemClock_Config();

	/* Initialize all configured peripherals */
	MX_GPIO_Init();
	MX_DMA_Init();
	MX_SPI1_Init();
	MX_ADC1_Init();
	MX_TIM1_Init();
	MX_TIM15_Init();
	MX_TIM2_Init();
	/* USER CODE BEGIN 2 */

	// Start polling ADC
	HAL_ADC_Start_DMA(&hadc1, adc_buf, 9);

	set_rotor();

	/* USER CODE END 2 */

	/* Infinite loop */
	/* USER CODE BEGIN WHILE */

	while (1)
	{
		/* USER CODE END WHILE */

		/* USER CODE BEGIN 3 */
		get_rotor_bemf(rotor_bemf);
		get_zero_crossing(rotor_bemf, prev_rotor_bemf);
		rotor_angle = get_rotor_angle(floating, rotor_speed);

		loop_pid(&speed_pid, rotor_speed, input_speed);

		drive_rotor(step, clamp(speed_pid.output, MIN_DUTY_CYCLE, 100));

		// Update previous rotor bemf
		for (int i = 0; i < 3; i++) {
			prev_rotor_bemf[i] = rotor_bemf[i];
		}
	}
	/* USER CODE END 3 */
}

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
/* USER CODE BEGIN 4 */

void HAL_TIM_IC_CaptureCallback(TIM_HandleTypeDef *htim)
{
	if (htim->Instance == TIM15)
	{
		uint32_t cycle_time = HAL_TIM_ReadCapturedValue(htim, TIM_CHANNEL_1);

		if (cycle_time == 0) {
			return;
		}

		double duty_cycle = (HAL_TIM_ReadCapturedValue(htim, TIM_CHANNEL_2) * 100.0) / cycle_time;

		// Convert duty cycle to rpm
		rotor_speed = map(duty_cycle, 0, 100, MIN_RPM, MAX_RPM);
	}
}

static uint8_t sign(double value) {
	if (value > 0) {
		return 1;
	}

	if (value < 0) {
		return -1;
	}

	return 0;
}

static float process_adc(uint32_t raw_value) {
	return (raw_value * ADC_RESOLUTION_12B) / 3.3;
}

static float process_current(double raw_value) {
	return (1.65 - raw_value) / (20000000); // ((V_ref (3.3) / 2) - raw_value) / (gain (20) * R_sense (1000000))
}

static uint8_t check_valid_bemf(double bemf_v) {
	if (bemf_v < BEMF_MIN_MARGIN) {
		return 1; // BEMF voltage is too small to read
	}

	if (bemf_v > adc_buf[SYS_VOLT_INDEX] - BEMF_MAX_MARGIN) {
		return 2; // BEMF is to close to sys voltage, probably not true BEMF
	}

	return 0;
}

static double clamp(double value, double min, double max) {
	if (value < min) {
		return min;
	}

	if (value > max) {
		return max;
	}

	return value;
}

static double map(double value, double in_min, double in_max, double out_min, double out_max) {
	return (value - in_min) * (out_max - out_min) / (in_max - in_min) + out_min;
}

static double get_rotor_angle(uint8_t floating, double rotor_speed) {
	double angle = phase_angles[floating];

	double rotor_time = HAL_GetTick() - zero_cross_time;
	angle += rotor_speed * (rotor_time / 60000); // Convert rotor time to minutes.

	return angle;
}

static void get_rotor_bemf(double *rotor_bemf_p) {
	float v_gnd = process_adc(adc_buf[V_GND_INDEX ]);

	// Phase A is floating
	if (floating == 0) {
		double voltage = process_adc(adc_buf[BEMF_A_INDEX]) - v_gnd;

		if (check_valid_bemf(voltage) == 1) { // BEMF is to small to detect, run startup sequence
			startup_sequence();
		}

		if (check_valid_bemf(voltage) == 2) { // BEMF is sys voltage, reading ADC at the wrong time
			return;
		}

		rotor_bemf_p[0] = voltage;
		return;
	}

	// Phase B is floating
	if (floating == 1) {
		double voltage = process_adc(adc_buf[BEMF_B_INDEX]) - v_gnd;

		if (check_valid_bemf(voltage) == 1) { // BEMF is to small to detect, run startup sequence
			startup_sequence();
		}

		if (check_valid_bemf(voltage) == 2) { // BEMF is sys voltage, reading ADC at the wrong time
			return;
		}

		rotor_bemf_p[1] = voltage;
		return;
	}

	// Phase C is floating
	if (floating == 2) {
		double voltage = process_adc(adc_buf[BEMF_C_INDEX]) - v_gnd;

		if (check_valid_bemf(voltage) == 1) { // BEMF is to small to detect, run startup sequence
			startup_sequence();
		}

		if (check_valid_bemf(voltage) == 2) { // BEMF is sys voltage, reading ADC at the wrong time
			return;
		}

		rotor_bemf_p[2] = voltage;
		return;
	}
}

static void get_rotor_current(double *rotor_current_p) {
	rotor_current_p[0] = process_current(process_adc(adc_buf[CURRENT_A_INDEX]));
	rotor_current_p[1] = process_current(process_adc(adc_buf[CURRENT_B_INDEX]));
	rotor_current_p[2] = process_current(process_adc(adc_buf[CURRENT_C_INDEX]));
}

static void drive_rotor(uint8_t step, double duty_cycle) {
	for (int i = 0; i < 3; i++) {
		if (dir * sequence[step][i] == 0) {
			floating = i;
			*sequence_tim[i][0] = 0;
			*sequence_tim[i][1] = 0;
			continue;
		}
		if (dir * sequence[step][i] == 1) {
			*sequence_tim[i][0] = duty_cycle;
			*sequence_tim[i][1] = 0;
			continue;
		}
		if (dir * sequence[step][i] == -1) {
			*sequence_tim[i][0] = 0;
			*sequence_tim[i][1] = duty_cycle;
			continue;
		}
	}
}

static void get_zero_crossing(double bemf[3], double prev_bemf[3]) {
	if (sign(rotor_bemf[floating] != sign(prev_rotor_bemf[floating]))) {
		step++;
		if (step > 6) {
			step = 0;
		}

		// Update speed when zero crossing is detected.
		double time = HAL_GetTick() - zero_cross_time;
		rotor_speed = 3 * (time / 60000); // Convert to RPM

		zero_cross_time = HAL_GetTick();
	}
}

static void set_rotor(void) {
	// Set rotor to 0 degrees

	drive_rotor(0, 100);

	HAL_Delay(SET_ROTOR_TIME);
}

static void startup_sequence(void) {
	drive_rotor(step, MIN_DUTY_CYCLE);

	HAL_Delay(STARTUP_DELAY);

	step++;
}

/* USER CODE END 4 */
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


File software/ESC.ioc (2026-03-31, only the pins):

Mcu.UserName=STM32G431CBTx
PA0.Signal=ADC1_IN1
PA1.Signal=ADC1_IN2
PA10.Signal=S_TIM1_CH3
PA11.Signal=S_TIM1_CH4
PA13.Signal=SYS_JTMS-SWDIO
PA14.Signal=SYS_JTCK-SWCLK
PA15.Signal=S_TIM2_CH1
PA2.Signal=ADC1_IN3
PA3.Signal=ADC1_IN4
PA4.Signal=SPI1_NSS
PA5.Signal=SPI1_SCK
PA6.Signal=SPI1_MISO
PA7.Signal=SPI1_MOSI
PA8.Signal=S_TIM1_CH1
PA9.Signal=S_TIM1_CH2
PB0.Signal=ADC1_IN15
PB1.Signal=ADC1_IN12
PB11.Signal=ADC1_IN14
PB12.Signal=ADC1_IN11
PB14.Signal=S_TIM15_CH1
PB15.Signal=S_TIM15_CH2
PB3.Signal=GPIO_Input
PB6.Signal=GPIO_Output
PB7.Signal=GPIO_Output
PB9.Signal=GPIO_Output
PF0-OSC_IN.Signal=RCC_OSC_IN
PF1-OSC_OUT.Signal=RCC_OSC_OUT

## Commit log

2026-03-19 added project files
    [ESC.kicad_pcb, ESC.kicad_sch]
2026-03-19 started schematic
    [ESC.kicad_sch]
2026-03-23 finished most of schematic
    [ESC.kicad_pcb, ESC.kicad_sch]
2026-03-23 layout first draft
    [ESC.kicad_pcb, ESC.kicad_sch]
2026-03-23 started routing schematic
    [ESC.kicad_pcb, ESC.kicad_sch]
2026-03-24 routing pcb
    [ESC.kicad_pcb, ESC.kicad_sch]
2026-03-24 updated to kicad 10.0
    [ESC.kicad_pcb, ESC.kicad_sch]
2026-03-24 moved regulator
    [ESC.kicad_pcb, ESC.kicad_sch]
2026-03-24 finished pcb
    [ESC.kicad_pcb, ESC.kicad_sch]
2026-03-25 added boot button and reset pad
    [ESC.kicad_pcb, ESC.kicad_sch]
2026-03-26 added filter cap to virtual gnd
    [ESC.kicad_pcb, ESC.kicad_sch]
2026-03-31 increase via and trace size
    [ESC.kicad_pcb]
2026-04-02 changed inductor size
    [ESC.kicad_pcb, ESC.kicad_sch, bom.csv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]
2026-04-04 beautified schematic
    [ESC.kicad_sch]
2026-04-04 updated silkscreen
    [ESC.kicad_pcb]
2026-04-04 updated production files
    [ESC.kicad_pcb, bom.csv, positions.csv]
2026-04-04 added step file
    [ESC.step]
2026-05-07 added new single side design
    [ESC.kicad_pcb, ESC.kicad_sch]
2026-05-08 added new regulator and gate driver
    [ESC.kicad_sch]
2026-05-08 added lables
    [ESC.kicad_sch]
2026-05-08 added lables but right this time
    [ESC.kicad_sch]
2026-05-08 fixed regulator cap value
    [ESC.kicad_sch]
2026-05-11 updated pcb
2026-05-11 made pcb layout
    [ESC.kicad_pcb, ESC.kicad_sch]
2026-05-11 added bulk capacitor
    [ESC.kicad_pcb, ESC.kicad_sch]
2026-05-15 routed pcb
    [ESC.kicad_pcb, ESC.kicad_sch]
2026-05-17 touched up pcb
    [ESC.kicad_pcb, ESC.kicad_sch]

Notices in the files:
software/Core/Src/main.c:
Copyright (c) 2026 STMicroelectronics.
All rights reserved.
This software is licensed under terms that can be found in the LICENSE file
